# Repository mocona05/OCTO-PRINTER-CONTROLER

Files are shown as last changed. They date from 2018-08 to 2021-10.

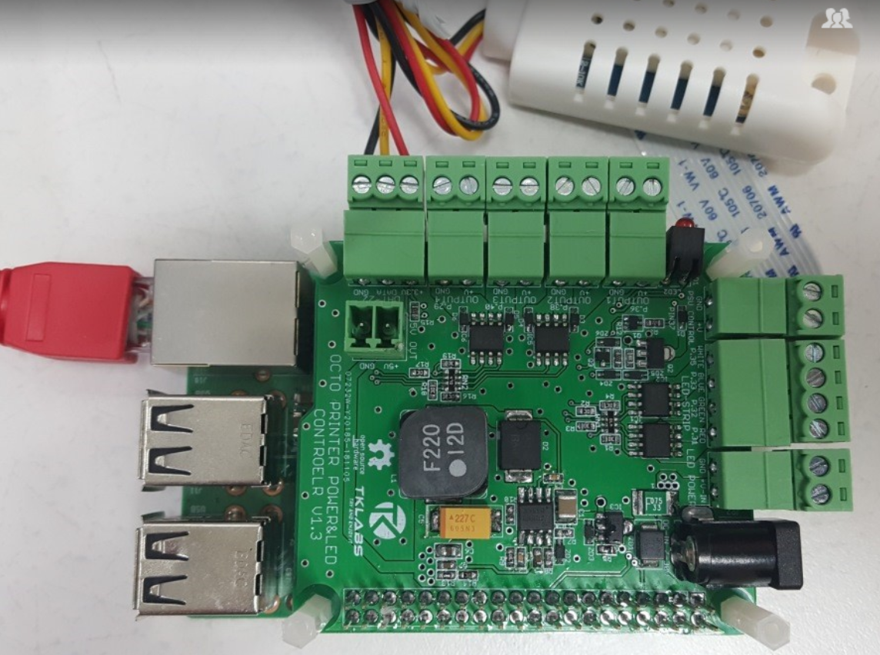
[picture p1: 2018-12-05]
image/octo printer.png

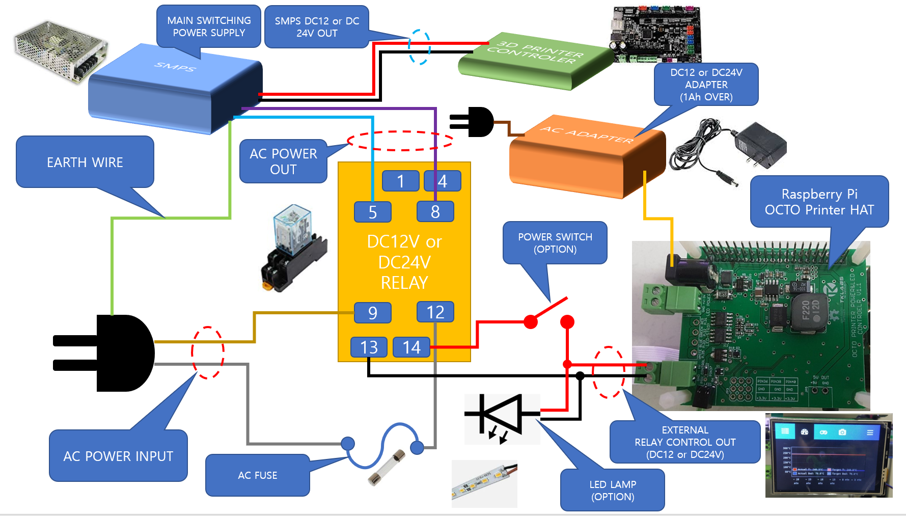
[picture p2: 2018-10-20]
image/WIRING.png

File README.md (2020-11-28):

# OCTO-PRINTER TFT-LCD HAT MOUDLE (3D PRINTER)

**1. DC 7~30V INPUT(DC12V or DC24V, 5V 4A OUT)**

**2. POWER SUPPLY UNIT CONTROL( EXTERNAL RELAY CONTROL 12V or 24V Relay)**

**3. RGBW LED STRIP CONTROL(RED, BLUE, GREEN, WHITE LED FET SWITCHING CONTROL)**

https://ko.aliexpress.com/item/33022691125.html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,searchweb201602_,searchweb201603_

**4. Raspberry SPI INTERFACE TFT-LCD & TOUCH SUPPORT**

https://ko.aliexpress.com/item/32233522592.html?spm=a2g0s.9042311.0.0.5f7c4c4dNYOjiv

**5. ENCLOSURE-CONTROL SUPPORT (HUMIDITY, TEMPERATURE MONITORING, OUTPUT RELAY 4CHANNEL CONTROL SUPPORT)**

**6. Raspberry Pi AP Cooling FAN(5V, PWM Speed Control)**

**7. Klipper ADXL345 Sensor Connector Bulit in(ADXL345 resonance sensor cannot be used simultaneously with SPI-LCD.)**

https://www.klipper3d.org/Measuring_Resonances.html

For more information, see WIKI.<br>
https://github.com/mocona05/OCTO-PRINTER-CONTROLER/wiki

Application of Octo Printer Shiled<br>
https://www.thingiverse.com/make:639404

OCTO Controler v1 4_PCB
OCTO Controler v1 4

octo printer
octo printer2
octo printer3

v1 2_sch
pcb_v1 2
wiring

v1 1_01
LCD module Pi TFT 3.5 inch (320*480) Touchscreen Display Module
v1 1_03
v1 1_02
v1 1_06
v1 1_v04
v1 1_v05
v1 1_v07
v1 1_v10

**TOUCH GHI SETTING**

OCTO PRINTER IMAGE DOWN LOAD
https://octoprint.org/download/

OCTO PRINTER IMAGE to SD MEMORY WRITE

https://www.raspberrypi.org/forums/viewtopic.php?t=131489
https://www.raspberrypi.org/forums/viewtopic.php?p=890408#p890408

**RASPBERRY PI FIRMWARE UPDATE**

`sudo rpi-update`

**RASPBERRY PI UPDATE**

`sudo apt-get update`<br>
`sudo apt-get upgrade`<br>

**RASPBERRY PI XWINDOWS INSTALL**

`sudo apt-get install --no-install-recommends xserver-xorg`<br>
`sudo apt-get install --no-install-recommends xinit`<br>
`sudo apt-get install raspberrypi-ui-mods`<br>

**xwindos auto login & Pi camera setting**

`sudo raspi-config`<br>
3.Boot-option -> B1 Desktop /CLI -> B4 Desktop Autologin

rpi-set01

Pi CAMERA SETUP (Raspberry pi camera used)
5. Interfacing Optin -> Pi Camera -> Yes
rpi-set02

7.Advanced Options -> A1 Expand Filesystem
rpi-set03

**TFT DRIVER INSTALL**

https://www.waveshare.com/wiki/3.5inch_RPi_LCD_(A)#Method_1._Driver_installation

`wget https://www.waveshare.com/w/upload/1/1e/LCD-show-180817.tar.gz`<br>

consol1

**DRIVER extractor**

`tar xvf LCD-show-180817.tar.gz`<br>
`cd LCD-show/`<br>
`chmod 777 LCD35-show`<br>
`./LCD35-show`<br>

**HDMI & TOUCH DRIVER INSTALL**

https://www.raspberrypi.org/forums/viewtopic.php?t=175616

`sudo apt-get install xinput-calibrator`<br>

**CHROMIUM INSTALL**

`sudo apt-get install unclutter`<br>
`sudo apt-get install xdotool`<br>

https://raspberrypi.stackexchange.com/questions/374/how-do-i-install-google-chrome

`sudo apt-get install chromium-browser`<br>

**CHROMIUM AUTO START SETTING**

https://www.raspberrypi.org/forums/viewtopic.php?t=163316

`sudo nano ~/.config/lxsession/LXDE-pi/autostart`<br>
`sudo -u pi chromium-browser --kiosk --incognito http://127.0.0.1 &`<br>

consol2

`sudo reboot`

connect at http://<your Raspberry pi's IP>

**PSU Control Plug In Setup**

gui01

**LED Strip Control Plug in Setup**

gui02

**TouchUI Plug in Setup**

gui03

**USB CAM Install(Option)**

https://github.com/jacksonliam/mjpg-streamer/

`sudo apt-get install subversion libjpeg8-dev libav-tools libv4l-dev cmake`<br>
`git clone https://github.com/jacksonliam/mjpg-streamer.git`<br>
`cd mjpg-streamer/mjpg-streamer-experimental`<br>
`export LD_LIBRARY_PATH=.`<br>
`sudo make`<br>

Connecting camera repeat command.

`ls /dev/video*`<br> 
(If you see the / dev / video0, then everything should be fine, go ahead)

ttps://github.com/foosel/OctoPrint/wiki/MJPG-Streamer-configuration

`sudo ./mjpg_streamer –i "./input_uvc.so –f 2 -y" -o "./output_http.so"`

check at http://<your Raspberry pi's IP>:8080/?action=stream

cam1

`sudo usermod -a -G video pi`<br>
(to allow user access to a device video, it is necessary to add it to the appropriate group)

`sudo make install`<br>
`cd ~`<br>
`sudo nano webcam-streamer`<br>

`#!/bin/bash`<br>
`Daemon=mjpg_streamer`<br>
`DaemonBase=/usr/local`<br>
`DaemonArgs="-i \"input_uvc.so –f 2 -y\" -o \"output_http.so\""`<br>
`case "" in`<br>
`start)`<br>
`eval LD_LIBRARY_PATH=${DaemonBase}/lib ${DaemonBase}/bin/${Daemon} ${DaemonArgs} >/dev/null 2>&1 &`<br>
`echo ": started"`<br>
`;;`<br>
`stop)`<br>
`pkill -x ${Daemon}`<br>
`echo ": stopped"`<br>
`;;`<br>
`*)`<br>
`echo "Usage:  {start|stop}" >&2`<br>
`;;`<br>
`Esac`<br>

cam02

`sudo chmod +x webcam-streamer`<br>
`sudo mv webcam-streamer /usr/local/bin/`<br>
`sudo nano ~/.octoprint/config.yaml`<br>

`system:`<br>
  `actions:`<br>
  `- action: streamon`<br>
    `command: sudo /usr/local/bin/webcam-streamer start`<br>
    `confirm: false`<br>
    `name: Start video stream`<br>
  `- action: streamoff`<br>
    `command: sudo /usr/local/bin/webcam-streamer stop`<br>
    `confirm: false`<br>
    `name: Stop video stream`<br>

cam03

cam04

**Auto start cam**

`sudo nano /etc/rc.local`<br>

`usr/local/bin/webcam-streamer start`<br>
(Just make sure to put it above the line that reads exit 0).

cam05

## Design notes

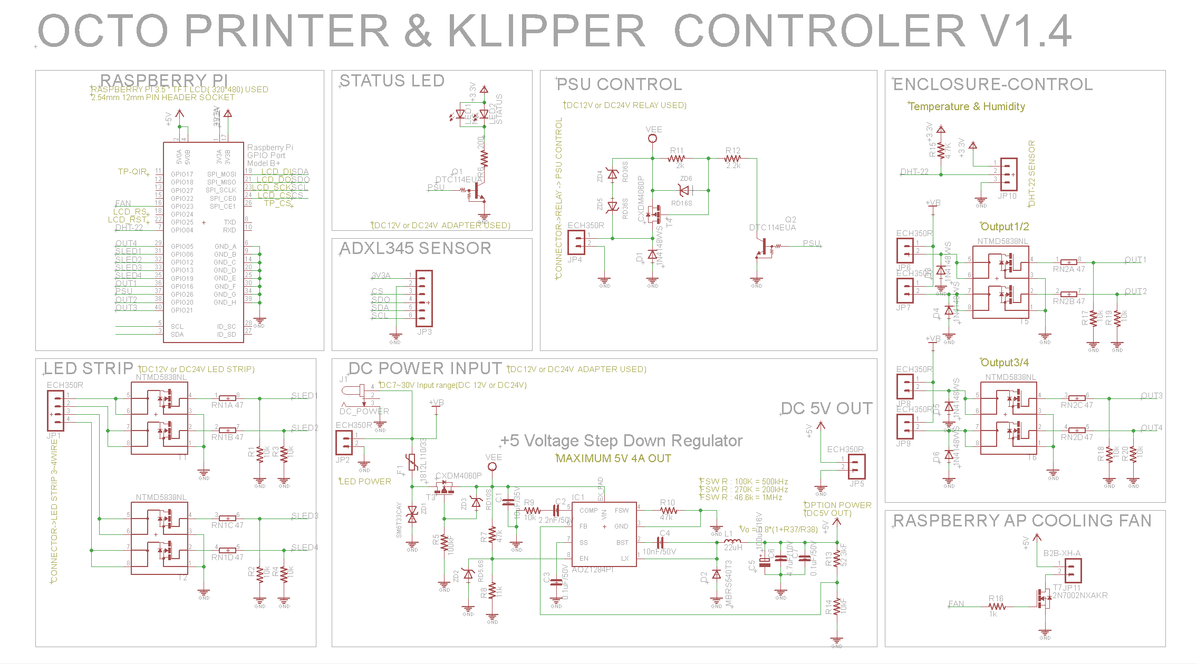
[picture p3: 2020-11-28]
image/OCTO Controler v1.4.png

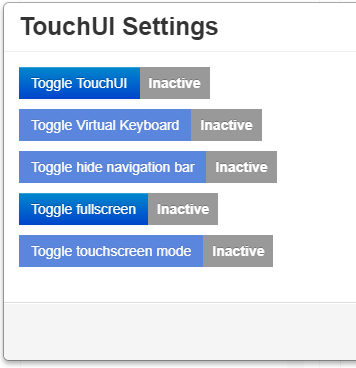
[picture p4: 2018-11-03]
image/touchUI.png

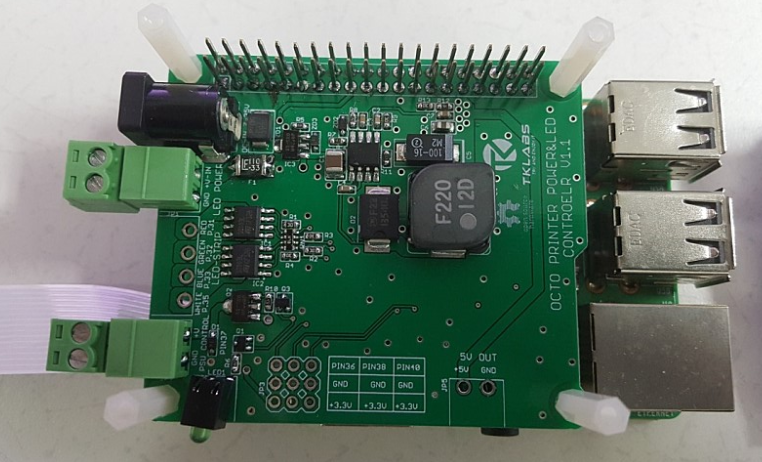
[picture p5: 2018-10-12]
image/V1.1_01.png

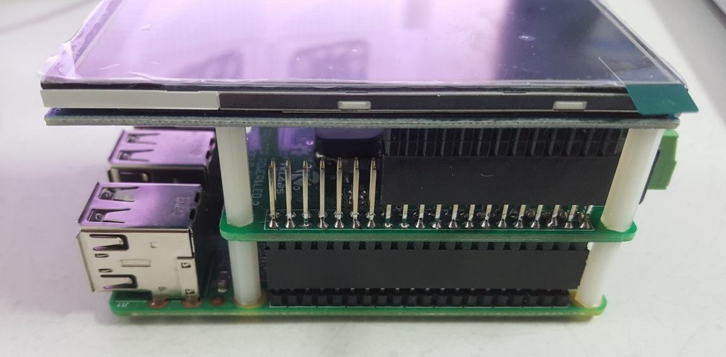
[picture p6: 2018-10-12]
image/V1.1_02.png

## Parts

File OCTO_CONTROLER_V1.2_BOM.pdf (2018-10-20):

No. | Parts | Value | Package | Device | Qty | Description
1 | R1, R2, R3, R4, R9 | 10kJ | R1608 | | 5 | SMD RESISTOR
2 | R11 | 2kJ | R1608 | | 1 | SMD RESISTOR
3 | R12 | 2.2kJ | R1608 | | 1 | SMD RESISTOR
4 | R13 | 52.3kF | R1608 | | 1 | SMD RESISTOR
5 | R5 | 100kJ | R1608 | | 1 | SMD RESISTOR
6 | R6 | 200J | R1608 | | 1 | SMD RESISTOR
7 | R7, R10 | 47kJ | R1608 | | 2 | SMD RESISTOR
8 | R8 | 11kJ | R1608 | | 1 | SMD RESISTOR
9 | R14 | 10kF | R1608 | | 1 | SMD RESISTOR
10 | RN1 | 47J | ARRAY R3216 | | 1 | ARRAY SMD RESISTOR
11 | C1 | 10uF/35V | C3225 | | 1 | CERAMIC CAP
12 | C2 | 2.2nF/50V | C1608 | | 1 | CERAMIC CAP
13 | C3 | 0.1uF/50V | C1608 | | 1 | CERAMIC CAP
14 | C4 | 10nF/50V | C1608 | | 1 | CERAMIC CAP
15 | C5 | 100uF/16V | C7343 | | 1 | TANTAL CAPACITOR
16 | C6 | 4.7uF/10V | C2012 | | 1 | CERAMIC CAP
17 | C7 | 0.1uF | C1608 | | 1 | CERAMIC CAP
18 | D1 | 1N4148WS | SOD323 | | 1 | DIODE
19 | D2 | MBRS540T3 | SMC | | 1 | SCHOTTKY DIODE
20 | ZD1 | SM6T33CAY | SMB | | 1 | TVS DIODE 33V
21 | ZD2 | RD5.6S | DSMM | | 1 | ZENER DIODE 5.6V
22 | ZD3 | RD10S | DSMM | | 1 | ZENER DIODE 47V
23 | ZD4, ZD5 | RD36S | DSMM | | 2 | ZENER DIODE 47V
24 | ZD6 | RD16S | DSMM | | 1 | ZENER DIODE 47V
25 | LED1 | NC | LED-1608 | | 1 | NOT SMD
26 | LED2 | 3FG2HD-T1 | | RED LED | 1 | BOARD MOUNT LED
27 | F1 | 1812L110/33 | 1812L | | 1 | POLY FUSE(HOLD 1.1A, MAX 33V)
28 | IC1, IC2 | NTMD5838NL | SO08 | | 2 | DUAL CHANNEL N-CH MOS FET
29 | IC3, Q2 | CXDM4060P | SOT89 | | 2 | P-CH MOS FET
30 | IC4 | AOZ1284PI | S08-EP1 | | 1 | SWITCHING REGULATOR
31 | L1 | 22uH | SHP1260P-F | | 1 | POWER INDUCTOR
32 | Q1, Q3 | DTC114EUA | SC59-BEC | | 2 | NPN Bias Resistor Transistor
33 | X1 | | 2.54mm DUAL *40PIN, 12mm | | 1 | 2.54mm DUAL PIN HEADER SOCKET 12mm
34 | J1 | | DC-005 | | 1 | DC JACK φ5.5mm
35 | JP2, JP4, JP5 | ECH350R-02 | 3.5mm PITCH 2PIN | | 3 | DINKLE PINHEADER 2PIN
36 | JP3 | 3*3, 2.54mm | 2.54mm PIN HEADER | PIN HEADER 3*3 | 1 | 3*3, 2.54mm RIGHT ANGLE PIN HEADER
37 | JP1 | ECH350R-04 | 3.5mm PITCH 3PIN | | 1 | DINKLE PINHEADER 4PIN
38 | | EC350V-02 | | | 3 | DINKLE CONNECTOR 2PIN
39 | | EC350V-04 | | | 1 | DINKLE CONNECTOR 4PIN
40 | TFT LCD | | | | 1 | 3.5 INCHI RASPBERRY LCD(320*480)
41 | PCB SUPPORT | 15mm | | | 4 | PCB SUPPORT M2
42 | PCB SUPPORT | 18mm | | | 4 | PCB SUPPORT M2

## OCTO PRINTER SHILED V1.2 BOM

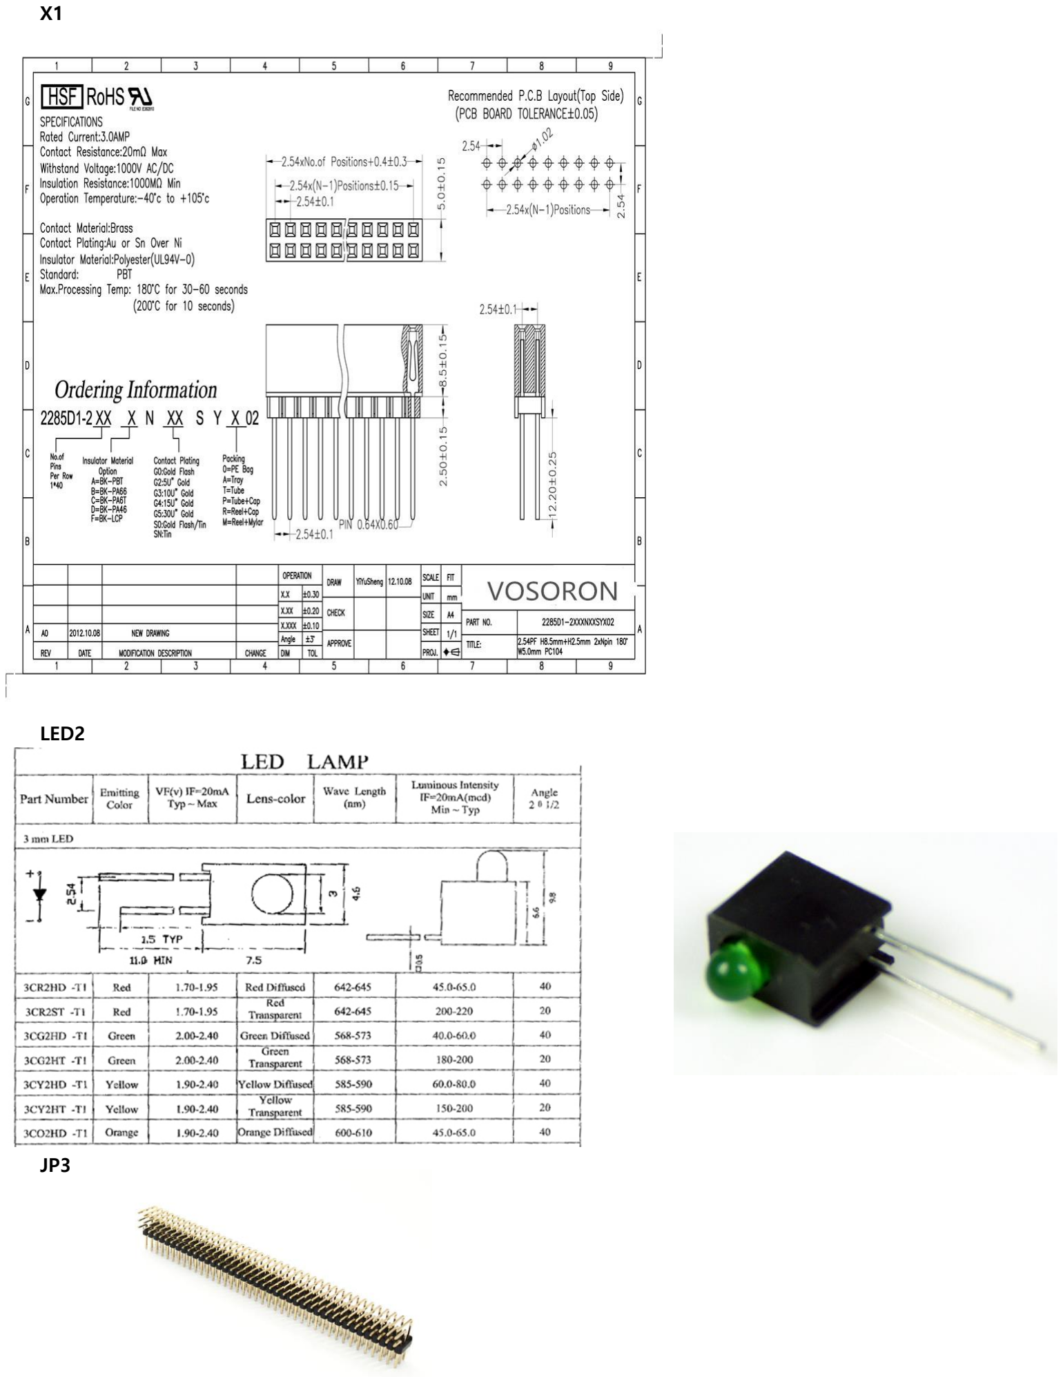
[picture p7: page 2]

X1

LED2

JP3 http://www.littelfuse.com/products/resettable-ptcs/surface-mount/1812l/1812l110_33.aspx

http://huijia-tech.com/upload/1230002737x-636397003.pdf

https://www.aliexpress.com/item/2PCS-2x40-PIN-double-Row-Straight-FEMALE-PIN-HEADER-2-54MM-PITCH-pin-long-12MM-Strip/32868136637.html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 (https://www.aliexpress.com/item/2PCS-2x40-PIN-double-Row-Straight-FEMALE-PIN-HEADER-2-54MM-PITCH-pin-long-12MM-Strip/32868136637.html)

https://www.dinkle.com/kr/terminal/ECH350R-XXPhttps://www.aliexpress.com/item/5Pcs-Gold-Plated-Pitch-2-54mm-3x40-Pin-120-Pin-Right-Angle-Male-Pin-Header-Strip/327023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 (https://www.aliexpress.com/item/5Pcs-Gold-Plated-Pitch-2-54mm-3x40-Pin-120-Pin-Right-Angle-Male-Pin-Header-Strip/32702387665.html) https://www.aliexpress.com/item/2PCS-2x40-PIN-double-Row-Straight-FEMALE-PIN-HEADER-2-54MM-PITCH-pin-long-12MMhttps://www.dinkle.com/en/terminal/EC350V-XXP

https://www.aliexpress.com/item/Free-shipping-LCD-module-Pi-TFT-3-5-inch-320-480-Touchscreen-Display-Module-TFT-for/32233522592.html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

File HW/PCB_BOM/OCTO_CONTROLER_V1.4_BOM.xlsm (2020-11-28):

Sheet: OCTO_CONTROLER_V1.2
OCTO PRINTER HAT V1.2 BOM
9f . V | Parts | Value | Package | Device | Qty | Description
1 | R1, R2, R3, R4, R9 | 10kJ | R1608 |  | 5 | SMD RESISTOR
2 | R11 | 2kJ | R1608 |  | 1 | SMD RESISTOR
3 | R12 | 2.2kJ | R1608 |  | 1 | SMD RESISTOR
4 | R13 | 52.3kF | R1608 |  | 1 | SMD RESISTOR
5 | R5 | 100kJ | R1608 |  | 1 | SMD RESISTOR
6 | R6 | 200J | R1608 |  | 1 | SMD RESISTOR
7 | R7, R10 | 47kJ | R1608 |  | 2 | SMD RESISTOR
8 | R8 | 11kJ | R1608 | sdf;m | 1 | SMD RESISTOR
9 | R14 | 10kF | R1608 |  | 1 | SMD RESISTOR
10 | RN1 | 47J | ARRAY R3216 |  | 1 | ARRAY SMD RESISTOR
11 | C1 | 10uF/35V | C3225 |  | 1 | CERAMIC CAP
12 | C2 | 2.2nF/50V | C1608 |  | 1 | CERAMIC CAP
13 | C3 | 0.1uF/50V | C1608 |  | 1 | CERAMIC CAP
14 | C4 | 10nF/50V | C1608 |  | 1 | CERAMIC CAP
15 | C5 | 100uF/16V | C7343 |  | 1 | TANTAL CAPACITOR
16 | C6 | 4.7uF/10V | C2012 |  | 1 | CERAMIC CAP
17 | C7 | 0.1uF | C1608 |  | 1 | CERAMIC CAP
18 | D1 | 1N4148WS | SOD323 |  | 1 | DIODE
19 | D2 | MBRS540T3 | SMC |  | 1 | SCHOTTKY DIODE
20 | ZD1 | SM6T33CAY | SMB |  | 1 | TVS DIODE 33V
21 | ZD2 | RD5.6S | DSMM |  | 1 | ZENER DIODE 5.6V
22 | ZD3 | RD10S | DSMM |  | 1 | ZENER DIODE 47V
23 | ZD4, ZD5 | RD36S | DSMM |  | 2 | ZENER DIODE 47V
24 | ZD6 | RD16S | DSMM |  | 1 | ZENER DIODE 47V
~~25~~ | ~~LED1~~ | ~~NC~~ | ~~LED-1608~~ |  | ~~1~~ | ~~NOT SMD~~
26 | LED2 | 3FG2HD-T1 |  | RED LED | 1 | BOARD MOUNT LED
27 | F1 | 1812L110/33 | 1812L |  | 1 | POLY FUSE(HOLD 1.1A, MAX 33V) | http://www.littelfuse.com/products/resettable-ptcs/surface-mount/1812l/1812l110_33.aspx
28 | IC1, IC2 | NTMD5838NL | SO08 |  | 2 | DUAL CHANNEL N-CH MOS FET
29 | IC3, Q2 | CXDM4060P | SOT89 |  | 2 | P-CH MOS FET
30 | IC4 | AOZ1284PI | S08-EP1 |  | 1 | SWITCHING REGULATOR
31 | L1 | 22uH | SHP1260P-F |  | 1 | POWER INDUCTOR | http://huijia-tech.com/upload/1230002737x-636397003.pdf
32 | Q1, Q3 | DTC114EUA | SC59-BEC |  | 2 | NPN Bias Resistor Transistor
33 | X1 |  | 2.54mm DUAL *40PIN, 12mm |  | 1 | 2.54mm DUAL PIN HEADER SOCKET 12mm | https://www.aliexpress.com/item/2PCS-2x40-PIN-double-Row-Straight-FEMALE-PIN-HEADER-2-54MM-PITCH-pin-long-12MM-Strip/32868136637.html
34 | J1 |  | DC-005 |  | 1 | DC JACK φ5.5mm
35 | JP2, JP4, JP5 | ECH350R-02 | 3.5mm PITCH 2PIN |  | 3 | DINKLE PINHEADER 2PIN | https://www.dinkle.com/kr/terminal/ECH350R-XXP
36 | JP3 | 3*3, 2.54mm | 2.54mm PIN HEADER | PIN HEADER 3*3 | 1 | 3*3, 2.54mm RIGHT ANGLE PIN HEADER | https://www.aliexpress.com/item/5Pcs-Gold-Plated-Pitch-2-54mm-3x40-Pin-120-Pin-Right-Angle-Male-Pin-Header-Strip/32702387665.html
37 | JP1 | ECH350R-04 | 3.5mm PITCH 3PIN |  | 1 | DINKLE PINHEADER 4PIN | https://www.aliexpress.com/item/2PCS-2x40-PIN-double-Row-Straight-FEMALE-PIN-HEADER-2-54MM-PITCH-pin-long-12MM-Strip/32868136637.html
38 |  | EC350V-02 |  |  | 3 | DINKLE CONNECTOR 2PIN | https://www.dinkle.com/en/terminal/EC350V-XXP
39 |  | EC350V-04 |  |  | 1 | DINKLE CONNECTOR 4PIN
40 | TFT LCD |  |  |  | 1 | 3.5 INCHI RASPBERRY LCD(320*480) | https://www.aliexpress.com/item/Free-shipping-LCD-module-Pi-TFT-3-5-inch-320-480-Touchscreen-Display-Module-TFT-for/32233522592.html
41 | PCB SUPPORT | 15mm |  |  | 4 | PCB SUPPORT M2
42 | PCB SUPPORT | 18mm |  |  | 4 | PCB SUPPORT M2
 | X1
 | LED2
 | JP3

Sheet: OCTO_CONTROLER_V1.3
OCTO PRINTER HAT V1.4 BOM
No. | Parts | Value | Package | Device | Qty | Description
1 | R1, R2, R3, R4, R9, R17, R18, R19, R20 | 10kJ | R1608 |  | 9 | SMD RESISTOR
2 | R11 | 2kJ | R1608 |  | 1 | SMD RESISTOR
3 | R12 | 2.2kJ | R1608 |  | 1 | SMD RESISTOR
4 | R13 | 52.3kF | R1608 |  | 1 | SMD RESISTOR
5 | R5 | 100kJ | R1608 |  | 1 | SMD RESISTOR
6 | R6 | 200J | R1608 |  | 1 | SMD RESISTOR
7 | R7, R10 | 47kJ | R1608 |  | 2 | SMD RESISTOR
8 | R8 | 11kJ | R1608 | sdf;m | 1 | SMD RESISTOR
9 | R14 | 10kF | R1608 |  | 1 | SMD RESISTOR
10 | R15 | 4.7k | R1608 |  | 1 | SMD RESISTOR
11 | R16 | 1k | R1608 |  | 1 | SMD RESISTOR
12 | RN1, RN2 | 47J | ARRAY R3216 |  | 2 | ARRAY SMD RESISTOR
13 | C1 | 10uF/35V | C3225 |  | 1 | CERAMIC CAP
14 | C2 | 2.2nF/50V | C1608 |  | 1 | CERAMIC CAP
15 | C3, C7 | 0.1uF/50V | C1608 |  | 2 | CERAMIC CAP
16 | C4 | 10nF/50V | C1608 |  | 1 | CERAMIC CAP
17 | C5 | 100uF/16V | C7343 |  | 1 | TANTAL CAPACITOR
18 | C6 | 4.7uF/10V | C2012 |  | 1 | CERAMIC CAP
19 | D1 | 1N4148WS | SOD323 |  | 1 | DIODE
20 | D2 | MBRS540T3 | SMC |  | 1 | SCHOTTKY DIODE
21 | ZD1 | SM6T33CAY | SMB |  | 1 | TVS DIODE 33V
22 | ZD2 | RD5.6S | DSMM |  | 1 | ZENER DIODE 5.6V
23 | ZD3 | RD10S | DSMM |  | 1 | ZENER DIODE 47V
24 | ZD4, ZD5 | RD36S | DSMM |  | 2 | ZENER DIODE 47V
25 | ZD6 | RD16S | DSMM |  | 1 | ZENER DIODE 47V
26 | ~~LED1~~ | ~~NC~~ | ~~LED-1608~~ |  | ~~1~~ | ~~NOT SMD~~
27 | LED2 | 3FG2HD-T1 |  | RED LED | 1 | BOARD MOUNT LED
28 | F1 | 1812L110/33 | 1812L |  | 1 | POLY FUSE(HOLD 1.1A, MAX 33V) | http://www.littelfuse.com/products/resettable-ptcs/surface-mount/1812l/1812l110_33.aspx
29 | T1, T2, T5, T6 | NTMD5838NL | SO08 |  | 4 | DUAL CHANNEL N-CH MOS FET
30 | T3, T4 | CXDM4060P | SOT89 |  | 2 | P-CH MOS FET
31 | T7 | 2N7002NXAKR | SOT23 |  | 2 | N-CH MOS FET
32 | IC1 | AOZ1284PI | S08-EP1 |  | 1 | SWITCHING REGULATOR
33 | L1 | 22uH | SHP1260P-F |  | 1 | POWER INDUCTOR | http://huijia-tech.com/upload/1230002737x-636397003.pdf
34 | Q1, Q2 | DTC114EUA | SC59-BEC |  | 2 | NPN Bias Resistor Transistor
35 | X1 |  | 2.54mm DUAL *40PIN, 12mm |  | 1 | 2.54mm DUAL PIN HEADER SOCKET 12mm | https://www.aliexpress.com/item/2PCS-2x40-PIN-double-Row-Straight-FEMALE-PIN-HEADER-2-54MM-PITCH-pin-long-12MM-Strip/32868136637.html
36 | J1 |  | DC-005 |  | 1 | DC JACK φ5.5mm
37 | JP2, JP4, JP5, JP6, JP7, JP8, JP9 | ECH350R-02 | 3.5mm PITCH 2PIN |  | 5 | DINKLE PINHEADER 2PIN | https://www.dinkle.com/kr/terminal/ECH350R-XXP
38 | JP3 | 3*3, 2.54mm | 2.54mm PIN HEADER | PIN HEADER 3*3 | 1 | 3*3, 2.54mm RIGHT ANGLE PIN HEADER | https://www.aliexpress.com/item/5Pcs-Gold-Plated-Pitch-2-54mm-3x40-Pin-120-Pin-Right-Angle-Male-Pin-Header-Strip/32702387665.html
39 | JP1 | ECH350R-04 | 3.5mm PITCH 3PIN |  | 1 | DINKLE PINHEADER 4PIN | https://www.aliexpress.com/item/2PCS-2x40-PIN-double-Row-Straight-FEMALE-PIN-HEADER-2-54MM-PITCH-pin-long-12MM-Strip/32868136637.html
40 | JP11 | B2B-XH-A | 2.54mm JST XH |  | 1 | JST 2.52mm 2PIN
41 |  | EC350V-02 |  |  | 6 |  | https://www.dinkle.com/en/terminal/EC350V-XXP
42 |  | EC350V-03 |  |  | 1 | DINKLE CONNECTOR 4PIN
43 |  | EC350V-04 |  |  | 1 | DINKLE CONNECTOR 4PIN
44 | TFT LCD |  |  |  | 1 | 3.5 INCHI RASPBERRY LCD(320*480) | https://www.aliexpress.com/item/Free-shipping-LCD-module-Pi-TFT-3-5-inch-320-480-Touchscreen-Display-Module-TFT-for/32233522592.html
45 | PCB SUPPORT | 15mm |  |  | 4 | PCB SUPPORT M2
46 | PCB SUPPORT | 18mm |  |  | 4 | PCB SUPPORT M2
 | X1
 | LED2
 | JP3
 | B2B-XH-A
 | ADXL345 SENSOR
 | https://ko.aliexpress.com/item/4000196862769.html

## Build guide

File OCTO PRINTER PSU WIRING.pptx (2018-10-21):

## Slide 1

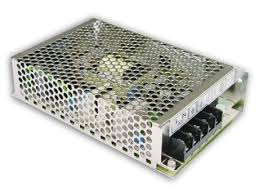
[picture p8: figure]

MAIN SWITCHING POWER SUPPLY

SMPS

SMPS DC12 or DC 24V OUT

3D PRINTER CONTROLER

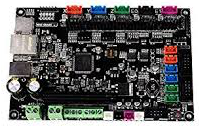
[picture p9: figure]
MKS 1.3ì ë í ì ´ë¯¸ì§ ê² ì ê²°ê³¼

DC12 or DC24V
ADAPTER
(1Ah OVER)

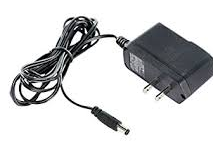
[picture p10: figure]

AC POWER OUT

AC ADAPTER

POWER SWITCH
(OPTION)

EARTH WIRE

DC12V or DC24V
RELAY

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
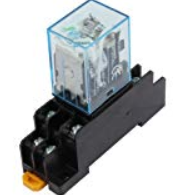
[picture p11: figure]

Raspberry Pi
OCTO Printer HAT

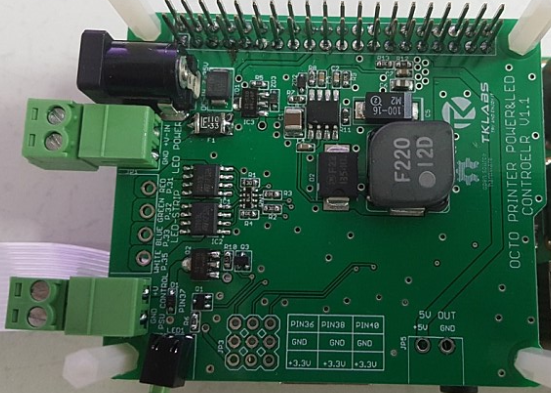
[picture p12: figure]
v1 1_01

EXTERNAL
RELAY CONTROL OUT
(DC12 or DC24V)

AC POWER INPUT

AC FUSE

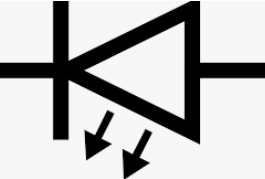
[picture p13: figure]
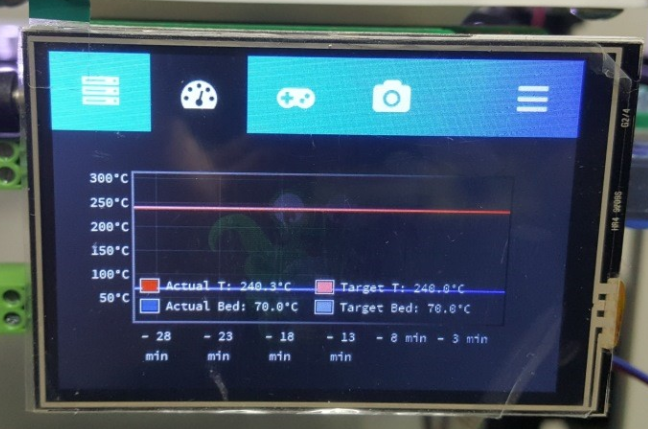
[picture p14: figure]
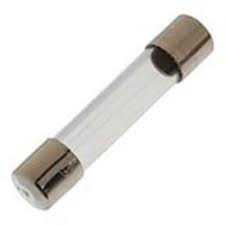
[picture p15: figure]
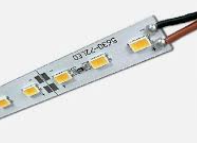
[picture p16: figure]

LED LAMP
(OPTION)

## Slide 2

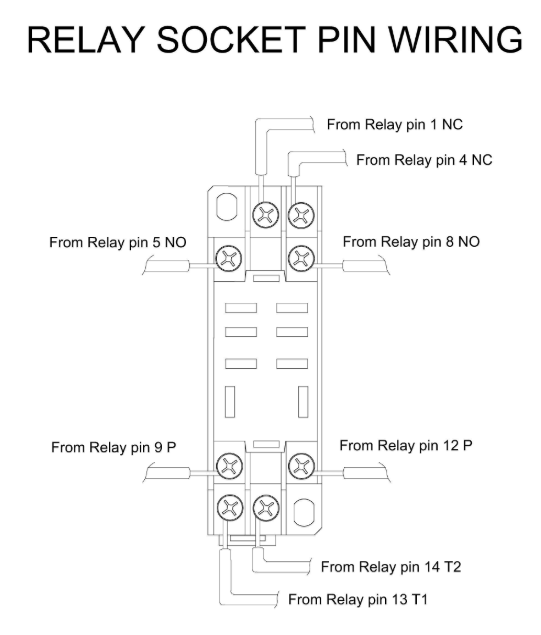
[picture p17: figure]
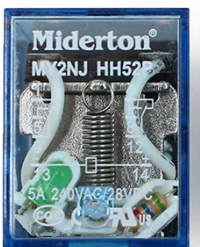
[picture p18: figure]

AC POWER OUT
(PSU UNIT)

AC POWER OUT
(PUS UNIT)

AC POWER IN
NETURAL

AC POWER IN
LIVE

+12 or 24V
(OCTO-PSU +OUT)

+12 or 24V

GND
(OCTO PI-PSU GND)

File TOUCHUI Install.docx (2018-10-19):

OCTO PRINTER IMAGE DOWN LOAD

https://octoprint.org/download/

OCTO PRINTER IMAGE to SD MEMORY WRITE

https://www.raspberrypi.org/forums/viewtopic.php?t=131489

https://www.raspberrypi.org/forums/viewtopic.php?p=890408#p890408

RASPBERRY PI FIRMWARE UPDATE

sudo rpi-update

RASPBERRY PI UPDATE

sudo apt-get update

sudo apt-get upgrade

RASPBERRY PI XWINDOWS INSTALL

sudo apt-get install --no-install-recommends xserver-xorg

sudo apt-get install --no-install-recommends xinit

sudo apt-get install raspberrypi-ui-mods

xwindos auto login & Pi camera setting

sudo raspi-config

3.Boot-option -> B1 Desktop /CLI -> B4 Desktop Autologin

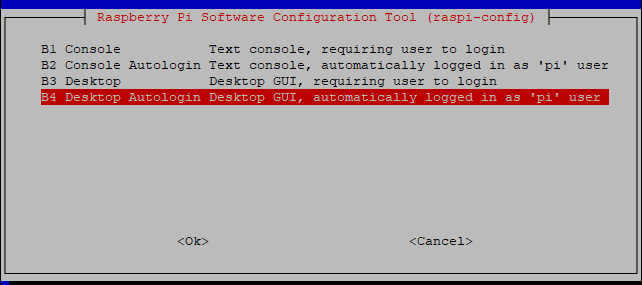
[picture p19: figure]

Pi CAMERA SETUP (Raspberry pi camera 사용시)

5. Interfacing Optin -> Pi Camera -> Yes

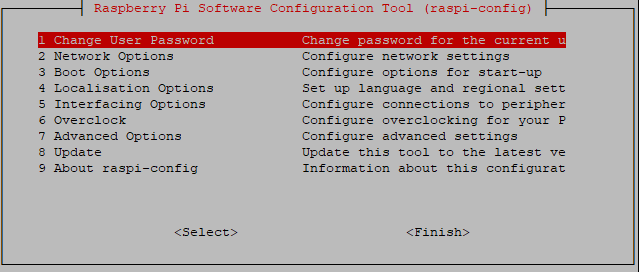
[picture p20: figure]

7.Advanced Options -> A1 Expand Filesystem

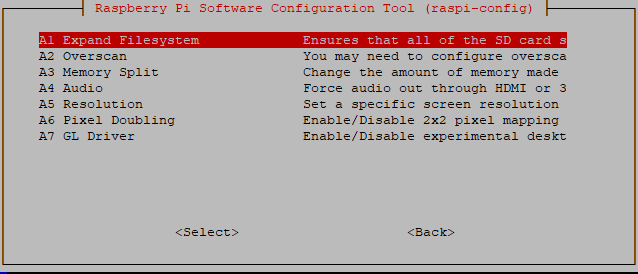
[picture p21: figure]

TFT DRIVER INSTALL

https://www.waveshare.com/wiki/3.5inch_RPi_LCD_(A)#Method_1._Driver_installation

wget https://www.waveshare.com/w/upload/1/1e/LCD-show-180817.tar.gz

DRIVER extractor

tar xvf LCD-show-180817.tar.gz

cd LCD-show/

chmod 777 LCD35-show

./LCD35-show

SPI-LCD & TOUCH DRIVER INSTALL

https://www.raspberrypi.org/forums/viewtopic.php?t=175616

sudo apt-get install xinput-calibrator

CHROMIUM INSTALL

sudo apt-get install unclutter
sudo apt-get install xdotool

https://raspberrypi.stackexchange.com/questions/374/how-do-i-install-google-chrome

sudo apt-get install chromium-browser

CHROMIUM AUTO START SETTING

https://www.raspberrypi.org/forums/viewtopic.php?t=163316

sudo nano ~/.config/lxsession/LXDE-pi/autostart

sudo -u pi chromium-browser --kiosk --incognito http://127.0.0.1 &

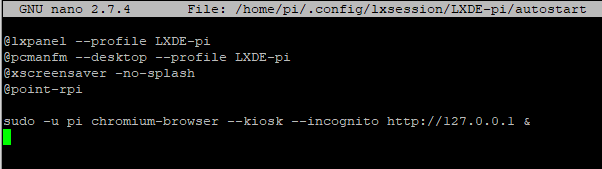
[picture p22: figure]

sudo reboot

PSU Control Plug In Setup

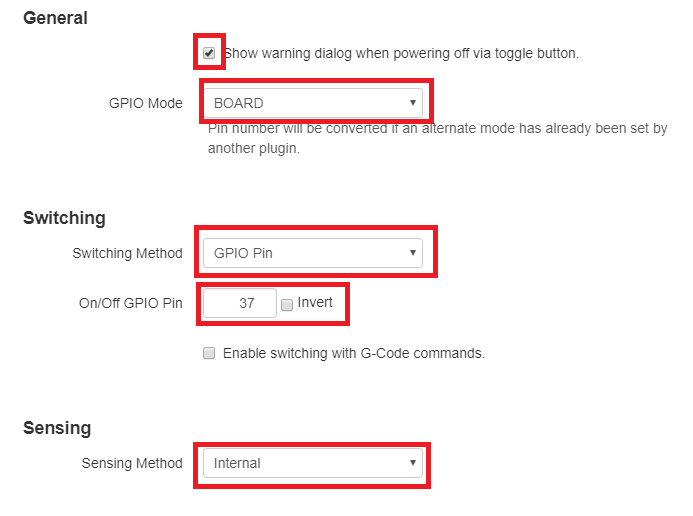
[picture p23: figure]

LED Strip Control Plug in Setup

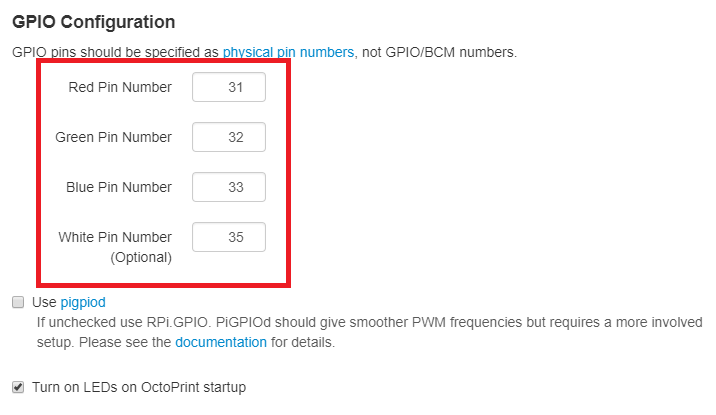
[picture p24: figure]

TouchUI Plug in Setup

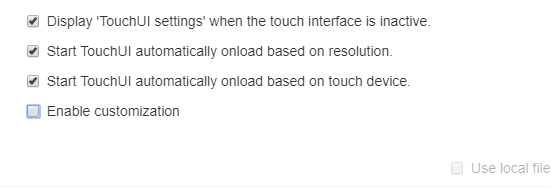
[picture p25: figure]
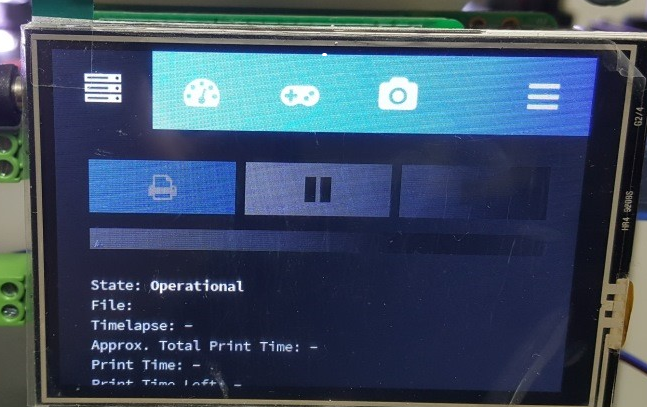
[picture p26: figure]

USB CAM Install(Option)

https://github.com/jacksonliam/mjpg-streamer/

sudo apt-get install subversion libjpeg8-dev libav-tools libv4l-dev cmake

git clone https://github.com/jacksonliam/mjpg-streamer.git

cd mjpg-streamer/mjpg-streamer-experimental

export LD_LIBRARY_PATH=.

sudo make

Connecting camera repeat command.

ls /dev/video* (If you see the / dev / video0, then everything should be fine, go ahead)

ttps://github.com/foosel/OctoPrint/wiki/MJPG-Streamer-configuration

sudo ./mjpg_streamer –i "./input_uvc.so –f 2 -y" -o "./output_http.so"

check at http://<your Raspberry pi's IP>:8080/?action=stream

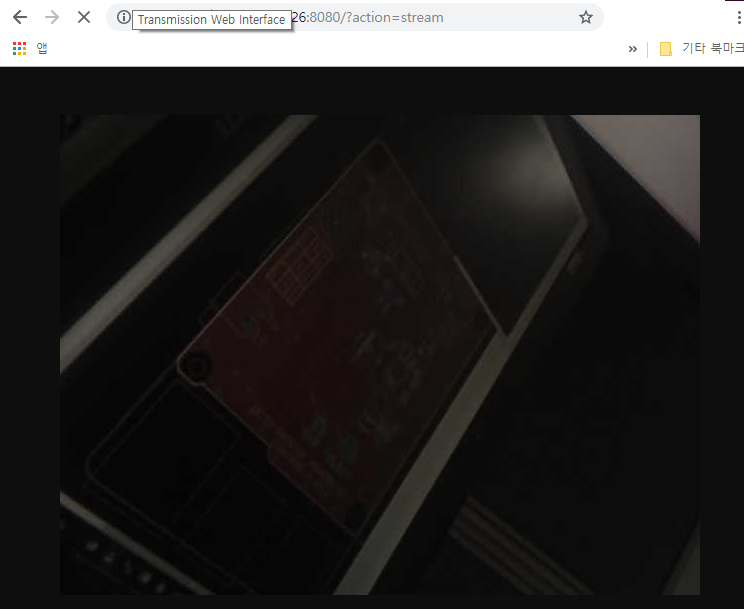
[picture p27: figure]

sudo usermod -a -G video pi

(to allow user access to a device video, it is necessary to add it to the appropriate group)

sudo make install

cd ~

sudo nano webcam-streamer

#!/bin/bash

Daemon=mjpg_streamer

DaemonBase=/usr/local

DaemonArgs="-i \"input_uvc.so –f 2 -y\" -o \"output_http.so\""

case "$1" in

start)

eval LD_LIBRARY_PATH=${DaemonBase}/lib ${DaemonBase}/bin/${Daemon} ${DaemonArgs} >/dev/null 2>&1 &

echo "$0: started"

;;

stop)

pkill -x ${Daemon}

echo "$0: stopped"

;;

*)

echo "Usage: $0 {start|stop}" >&2

;;

Esac

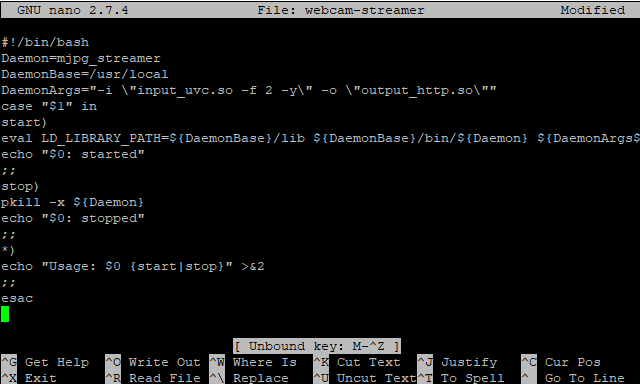
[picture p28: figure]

sudo chmod +x webcam-streamer

sudo mv webcam-streamer /usr/local/bin/

sudo nano ~/.octoprint/config.yaml

system:

actions:

- action: streamon

command: sudo /usr/local/bin/webcam-streamer start

confirm: false

name: Start video stream

- action: streamoff

command: sudo /usr/local/bin/webcam-streamer stop

confirm: false

name: Stop video stream

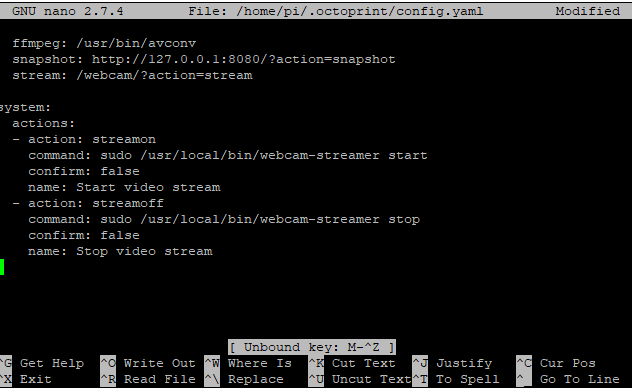
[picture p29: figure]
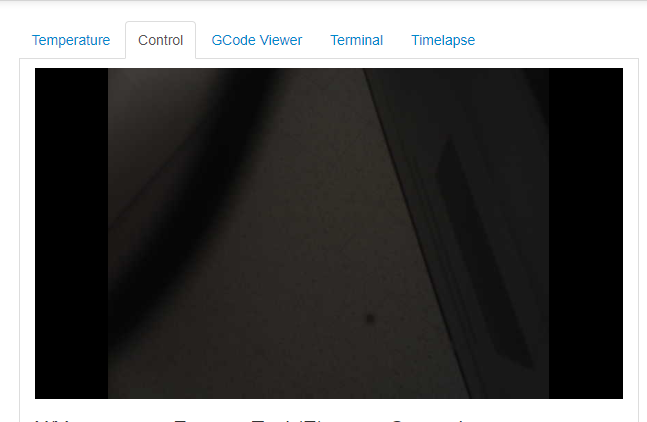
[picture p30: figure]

Auto start cam

sudo nano /etc/rc.local

usr/local/bin/webcam-streamer start

(Just make sure to put it above the line that reads exit 0).

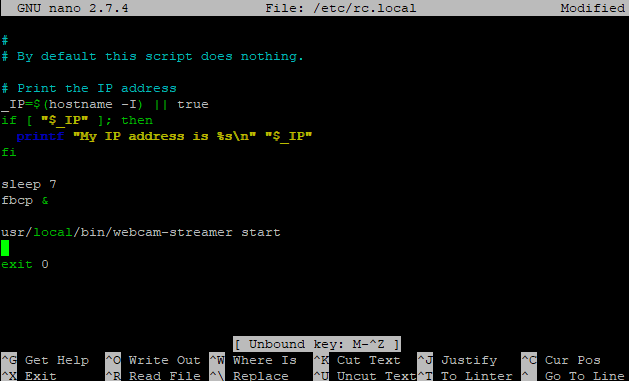
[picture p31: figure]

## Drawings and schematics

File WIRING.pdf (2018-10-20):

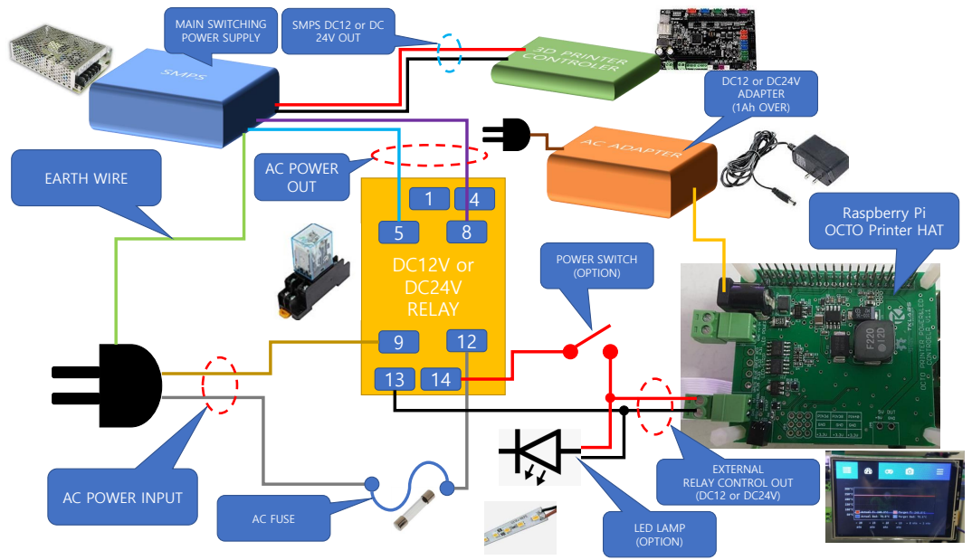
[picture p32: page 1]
DC12V or DC24V RELAY; DC12 or DC24V ADAPTER (1Ah OVER); MAIN SWITCHING POWER SUPPLY; POWER SWITCH (OPTION); AC FUSE; EARTH WIRE; AC POWER OUT; LED LAMP (OPTION)

SMPS DC12 or DC
24V OUT

Raspberry Pi
OCTO Printer HAT

EXTERNAL
RELAY CONTROL OUT

AC POWER INPUT

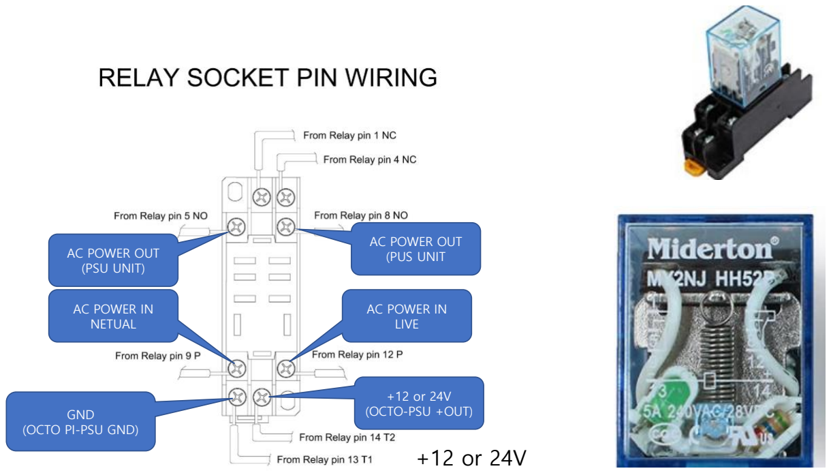
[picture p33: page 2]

# +12 or 24V

+12 or 24V
GND | (OCTO-PSU +OUT)
(OCTO PI-PSU GND)

AC POWER IN
NETUAL

AC POWER IN
LIVE

AC POWER OUT
AC POWER OUT | (PUS UNIT
(PSU UNIT)

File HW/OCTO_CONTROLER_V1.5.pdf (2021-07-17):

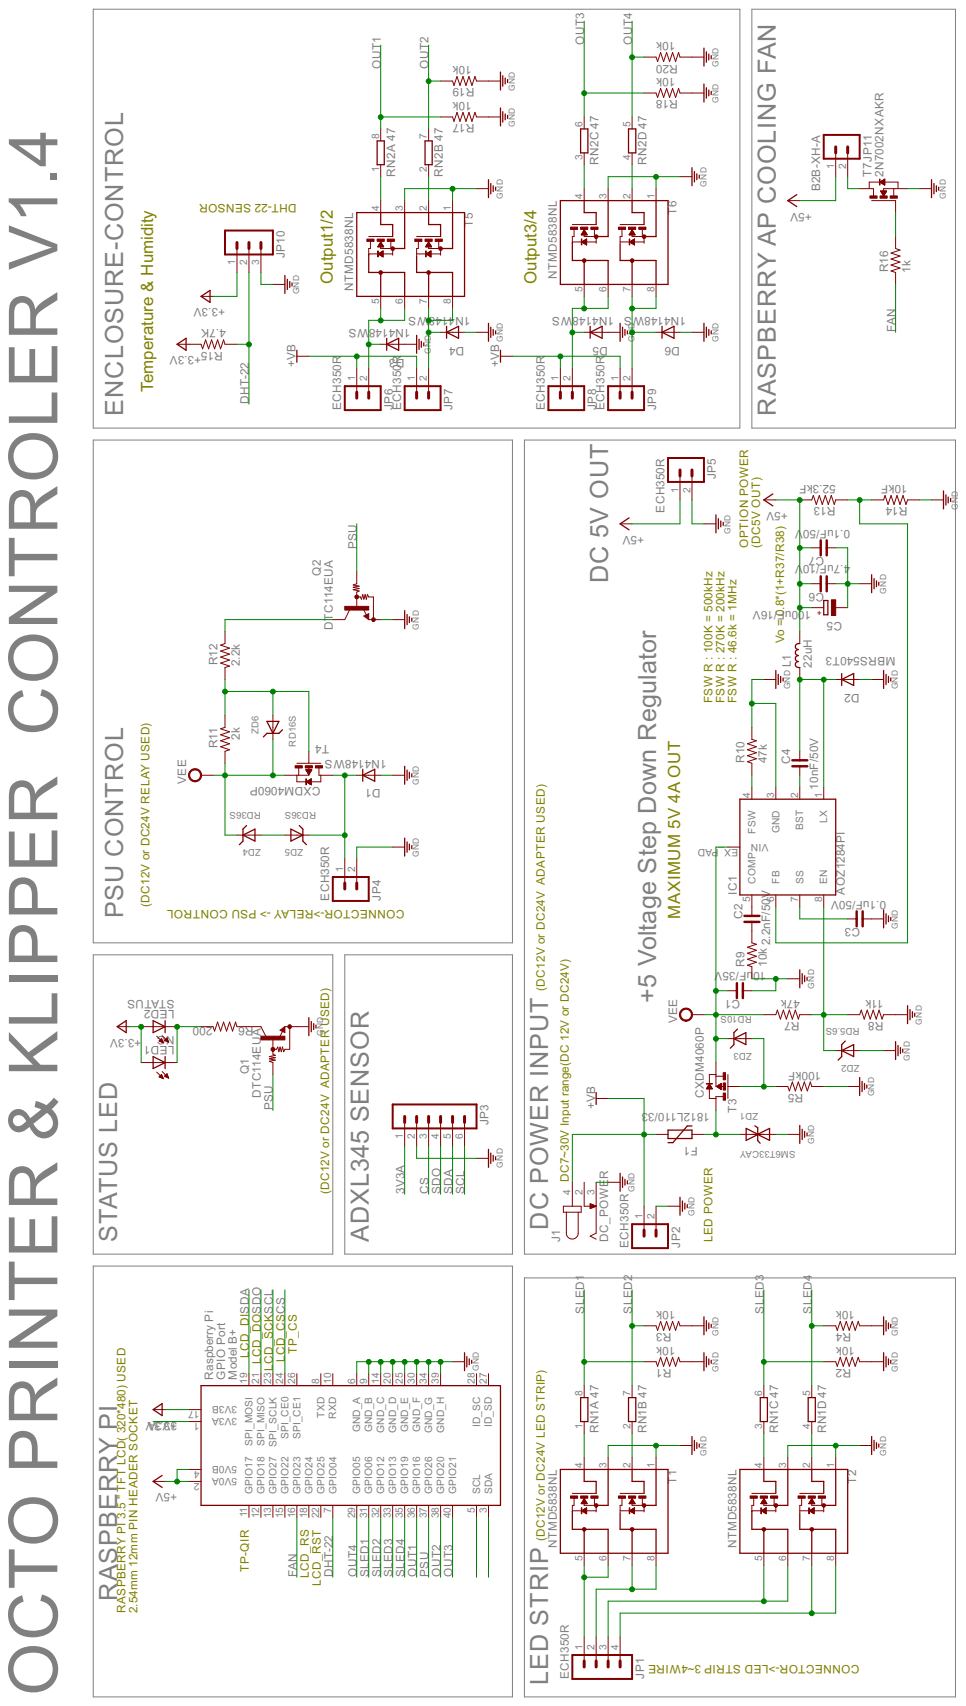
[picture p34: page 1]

2.54mm 12mm PIN HEADER SOCKET ROSNES 22- THD

GND GND

Raspberry Pi GPIO Port Model B+ 2k DTC114EUA

(DC12V or DC24V LED STRIP) (DC12V or DC24V ADAPTER USED)

DC7~30V Input range(DC 12V or DC24V)

RASPBERRY PI 3.5 " TFT LCD( 320*480) USED

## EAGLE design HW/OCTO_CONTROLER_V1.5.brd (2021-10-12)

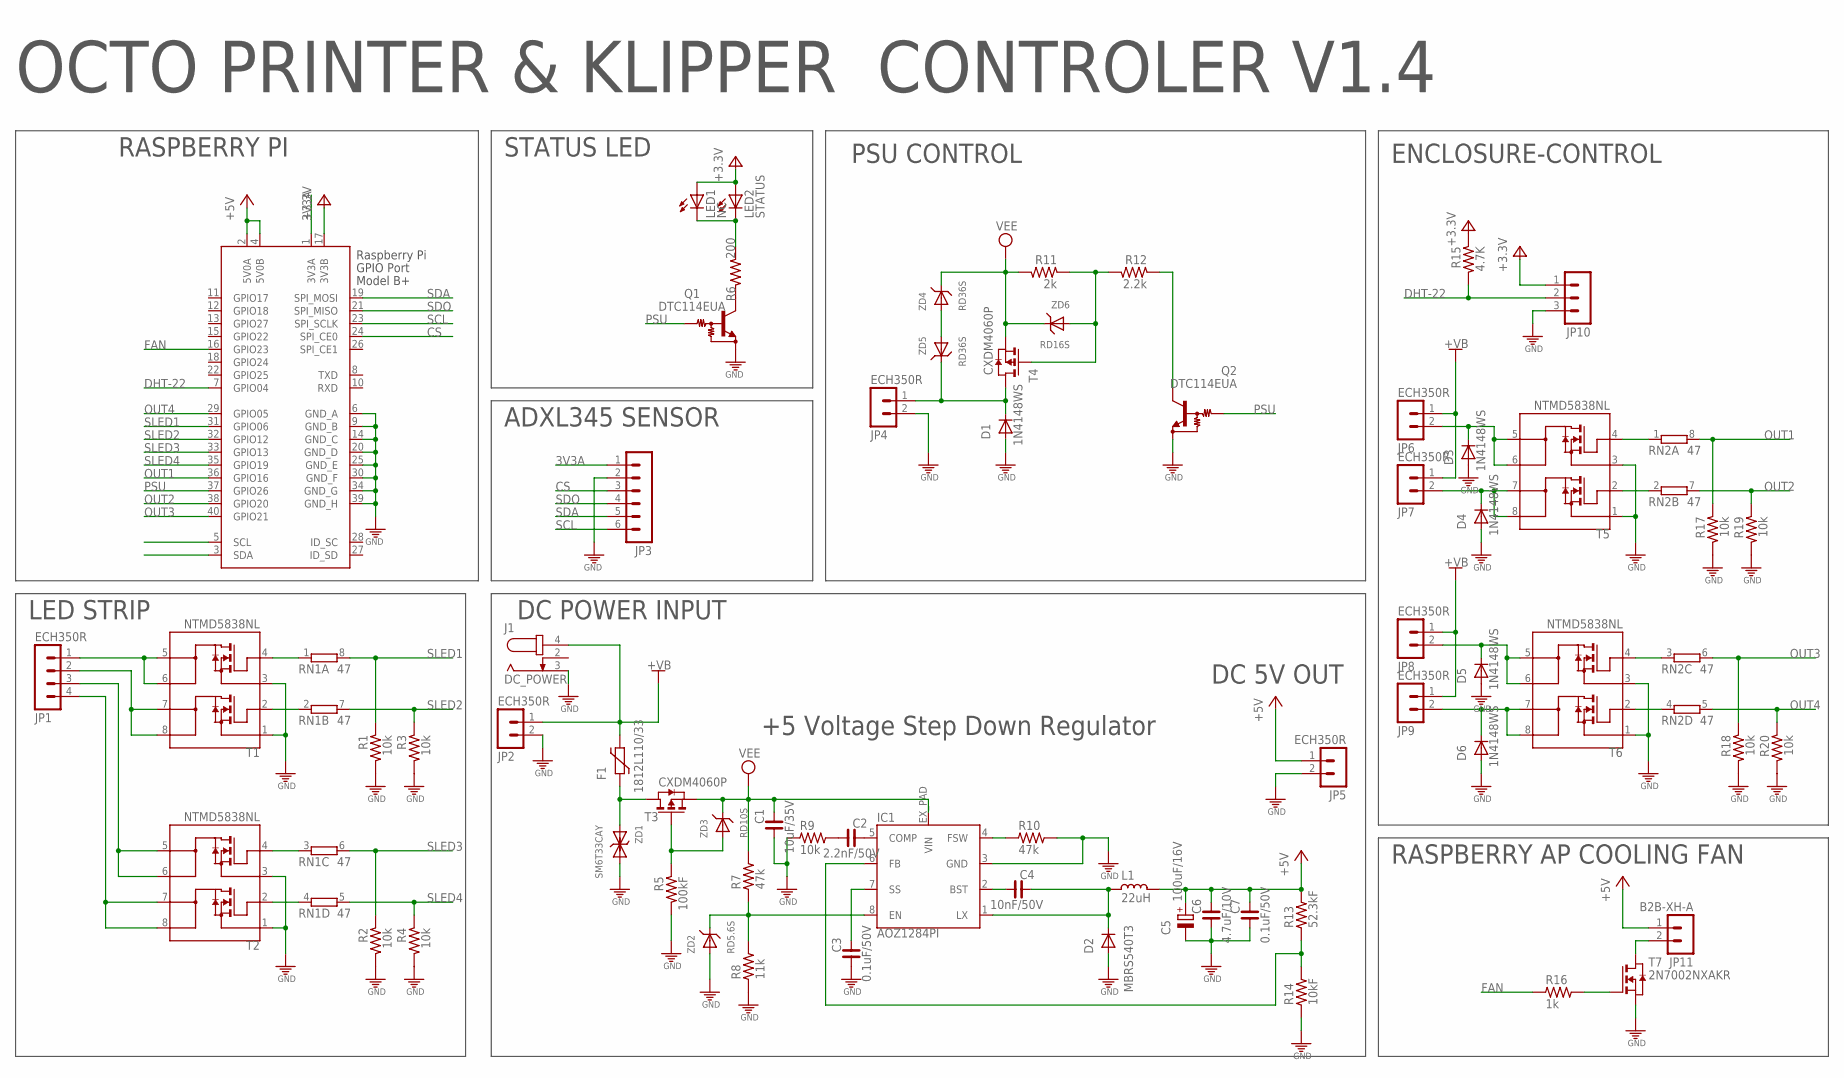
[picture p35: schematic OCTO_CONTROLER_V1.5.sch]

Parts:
C1: 10uF/35V; C3225
C2: 2.2nF/50V; C0603
C3, C7: 0.1uF/50V; C0603
C4: 10nF/50V; C0603
C5: 100uF/16V; D/7343-31W
C6: 4.7uF/10V; C2012
D1, D3, D4, D5, D6: 1N4148WS; SOD323
D2: MBRS540T3; SMC
F1: 1812L110/33; 1812L
IC1: AOZ1284PI; S08-EP1
J1: DC_POWER; DC-005
JP1: ECH350R; ECH350R-04
JP2, JP4, JP6, JP7, JP8, JP9: ECH350R; ECH350R-02
JP3: MA06-1SMALL; MA06-1-S
JP5: ECH350R; ECH350V-02
JP10: MA03-1ECH350R; ECH350R-03
JP11: B2B-XH-A; MOLEX5267-02
L1: 22uH; SHP1260P-F
LED1: NC; LED-1608
LED2: STATUS; 3FG2HD-T1
Q1, Q2: DTC114EUA; SC59-BEC
R1, R2, R3, R4, R9, R17, R18, R19, R20: 10k; R0603
R5: 100kF; R0603
R6: 200; R0603
R7, R10: 47k; R0603
R8: 11k; R0603
R11: 2k; R0603
R12: 2.2k; R0603
R13: 52.3kF; R0603
R14: 10kF; R0603
R15: 4.7K; R0603
R16: 1k; R0603
RN1, RN2: 47; ARRAY_R3216
T1, T2, T5, T6: NTMD5838NL; SO08
T3, T4: CXDM4060P; SOT89
T7: 2N7002NXAKR; SOT23
X1: RASPI_BOARD_B+#_F; RASPI_BOARD_B+_FULL
ZD1: SM6T33CAY; SMB
ZD2: RD5.6S; DSMM
ZD3: RD10S; DSMM
ZD4, ZD5: RD36S; DSMM
ZD6: RD16S; DSMM

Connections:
3V3: JP10.1, LED1.A, LED2.A, R15.1, X1.17 (3V3B)
3V3A: JP3.1, X1.1 (3V3A)
+5V: C5.+, C6.1, C7.1, JP5.1, JP11.1, L1.1, R13.2, X1.2 (5V0A), X1.4 (5V0B)
+12V: F1.P$2 (2), J1.4 (3), JP2.1, JP6.1, JP7.1, JP8.1, JP9.1
CS: JP3.3, X1.24 (SPI_CE0)
DC-IN: F1.P$1 (1), T3.2 (D), T3.2@1 (D), ZD1.A
DHT-22: JP10.2, R15.2, X1.7 (GPIO04)
FAN: R16.1, X1.16 (GPIO23)
GND: C1.2, C3.2, C5.-, C6.2, C7.2, D1.A, D2.A, D3.A, D4.A, D5.A, D6.A, IC1.3 (GND), J1.3 (1), JP2.2, JP3.2, JP4.2, JP5.2, JP10.3, Q1.1 (GND), Q2.1 (GND), R1.2, R2.2, R3.2, R4.2, R5.2, R8.1, R9.1, R10.2, R14.1, R17.2, R18.2, R19.2, R20.2, T1.1, T1.3, T2.1, T2.3, T5.1, T5.3, T6.1, T6.3, T7.S, X1.6 (GND_A), X1.9 (GND_B), X1.14 (GND_C), X1.20 (GND_D), X1.25 (GND_E), X1.30 (GND_F), X1.34 (GND_G), X1.39 (GND_H), ZD1.C (K), ZD2.A
unnamed: R11.1, R12.2, T4.3 (G), ZD6.A
unnamed: LED1.C, LED2.K (C), R6.1
unnamed: ZD4.A, ZD5.A
unnamed: RN1.2 (1), T1.2
unnamed: RN1.1, T1.4
unnamed: RN1.4 (1), T2.2
unnamed: JP11.2, T7.D
unnamed: R16.2, T7.G
unnamed: IC1.6 (FB), R13.1, R14.2
unnamed: RN1.3 (1), T2.4
unnamed: C4.2, IC1.2 (BST)
unnamed: D1.C, JP4.1, T4.2 (D), T4.2@1 (D), ZD5.C
unnamed: RN2.2 (1), T5.2
unnamed: RN2.1, T5.4
unnamed: D3.C, JP6.2, T5.5, T5.6
unnamed: D4.C, JP7.2, T5.7, T5.8
unnamed: RN2.4 (1), T6.2
unnamed: RN2.3 (1), T6.4
unnamed: C4.1, D2.C, IC1.1 (LX), L1.2
unnamed: IC1.4 (FSW), R10.1
unnamed: C3.1, IC1.7 (SS)
unnamed: IC1.8 (EN), R7.1, R8.2, ZD2.C
unnamed: C2.1, IC1.5 (COMP)
unnamed: Q2.3 (OUT), R12.1
unnamed: D5.C, JP8.2, T6.5, T6.6
unnamed: C2.2, R9.2
unnamed: D6.C, JP9.2, T6.7, T6.8
unnamed: Q1.3 (OUT), R6.2
unnamed: R5.1, T3.3 (G), ZD3.A
OUT1: R17.1, RN2.8 (2), X1.36 (GPIO16)
OUT2: R19.1, RN2.7 (2), X1.38 (GPIO20)
OUT3: R18.1, RN2.6 (2), X1.40 (GPIO21)
OUT4: R20.1, RN2.5 (2), X1.29 (GPIO05)
PSU: Q1.2 (IN), Q2.2 (IN), X1.37 (GPIO26)
S-LED1: JP1.1, T1.5, T1.6
S-LED2: JP1.2, T1.7, T1.8
S-LED3: JP1.3, T2.5, T2.6
S-LED4: JP1.4, T2.7, T2.8
SCL: JP3.6, X1.23 (SPI_SCLK)
SDA: JP3.5, X1.19 (SPI_MOSI)
SDO: JP3.4, X1.21 (SPI_MISO)
SLED1: R1.1, RN1.8 (2), X1.31 (GPIO06)
SLED2: R3.1, RN1.7 (2), X1.32 (GPIO12)
SLED3: R2.1, RN1.6 (2), X1.33 (GPIO13)
SLED4: R4.1, RN1.5 (2), X1.35 (GPIO19)
VEE: C1.1, IC1.EX_PAD (VIN), R7.2, R11.2, T3.1 (S), T4.1 (S), ZD3.C, ZD4.C, ZD6.C

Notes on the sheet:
OCTO PRINTER & KLIPPER CONTROLER V1.4
RASPBERRY PI
+5 Voltage Step Down Regulator
DC POWER INPUT
PSU CONTROL
STATUS LED
LED STRIP
DC 5V OUT
ENCLOSURE-CONTROL
ADXL345 SENSOR
RASPBERRY AP COOLING FAN

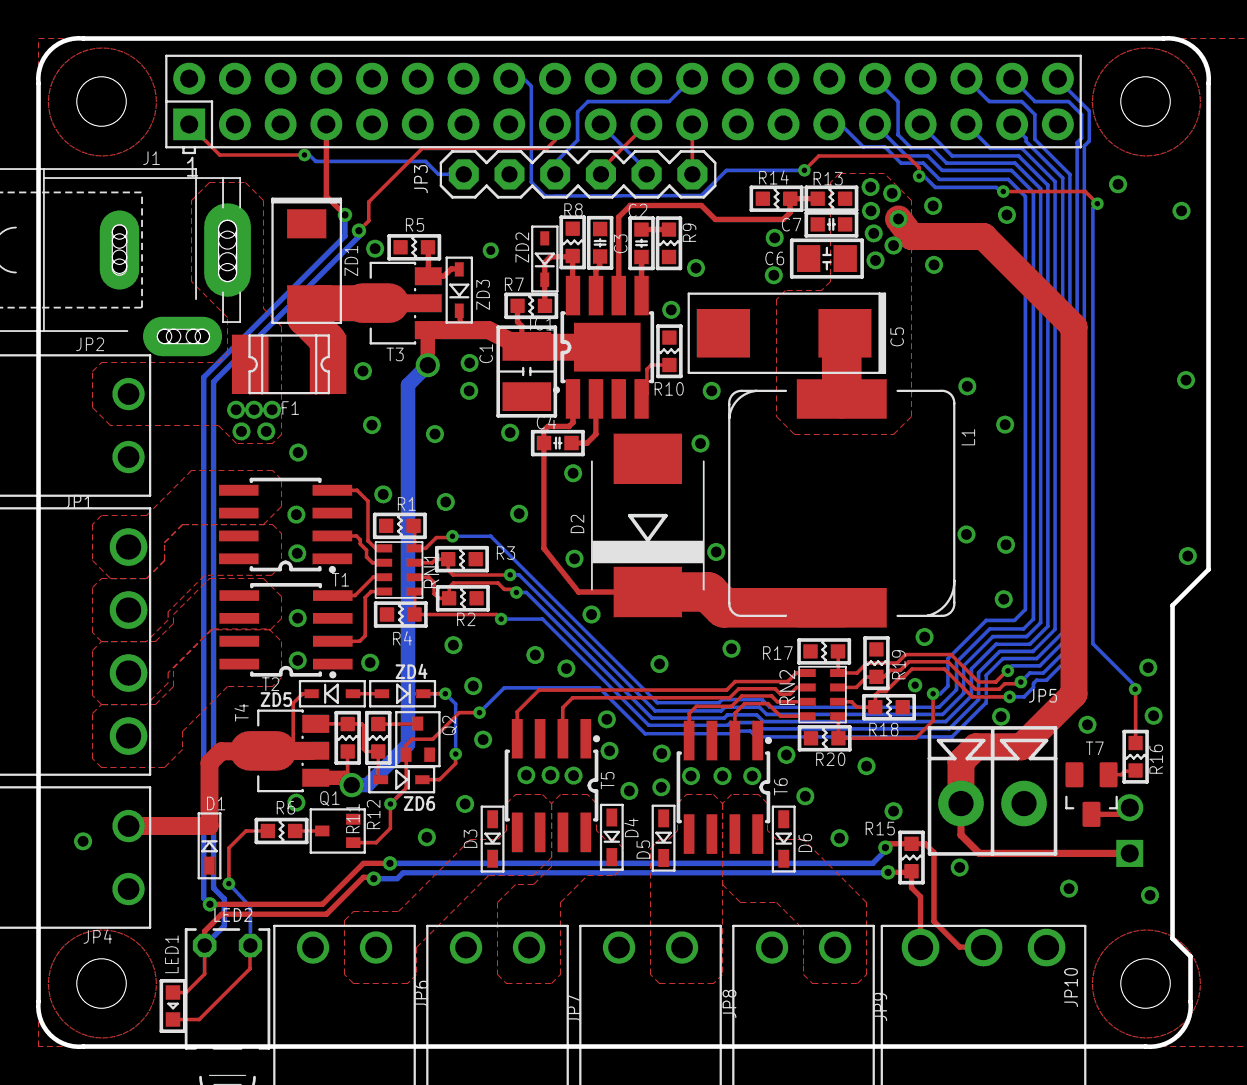
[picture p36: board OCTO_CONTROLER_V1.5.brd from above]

Board: 2 copper layers, 65.0 x 56.0 mm, 68 parts (1 on the bottom side), 55 nets.

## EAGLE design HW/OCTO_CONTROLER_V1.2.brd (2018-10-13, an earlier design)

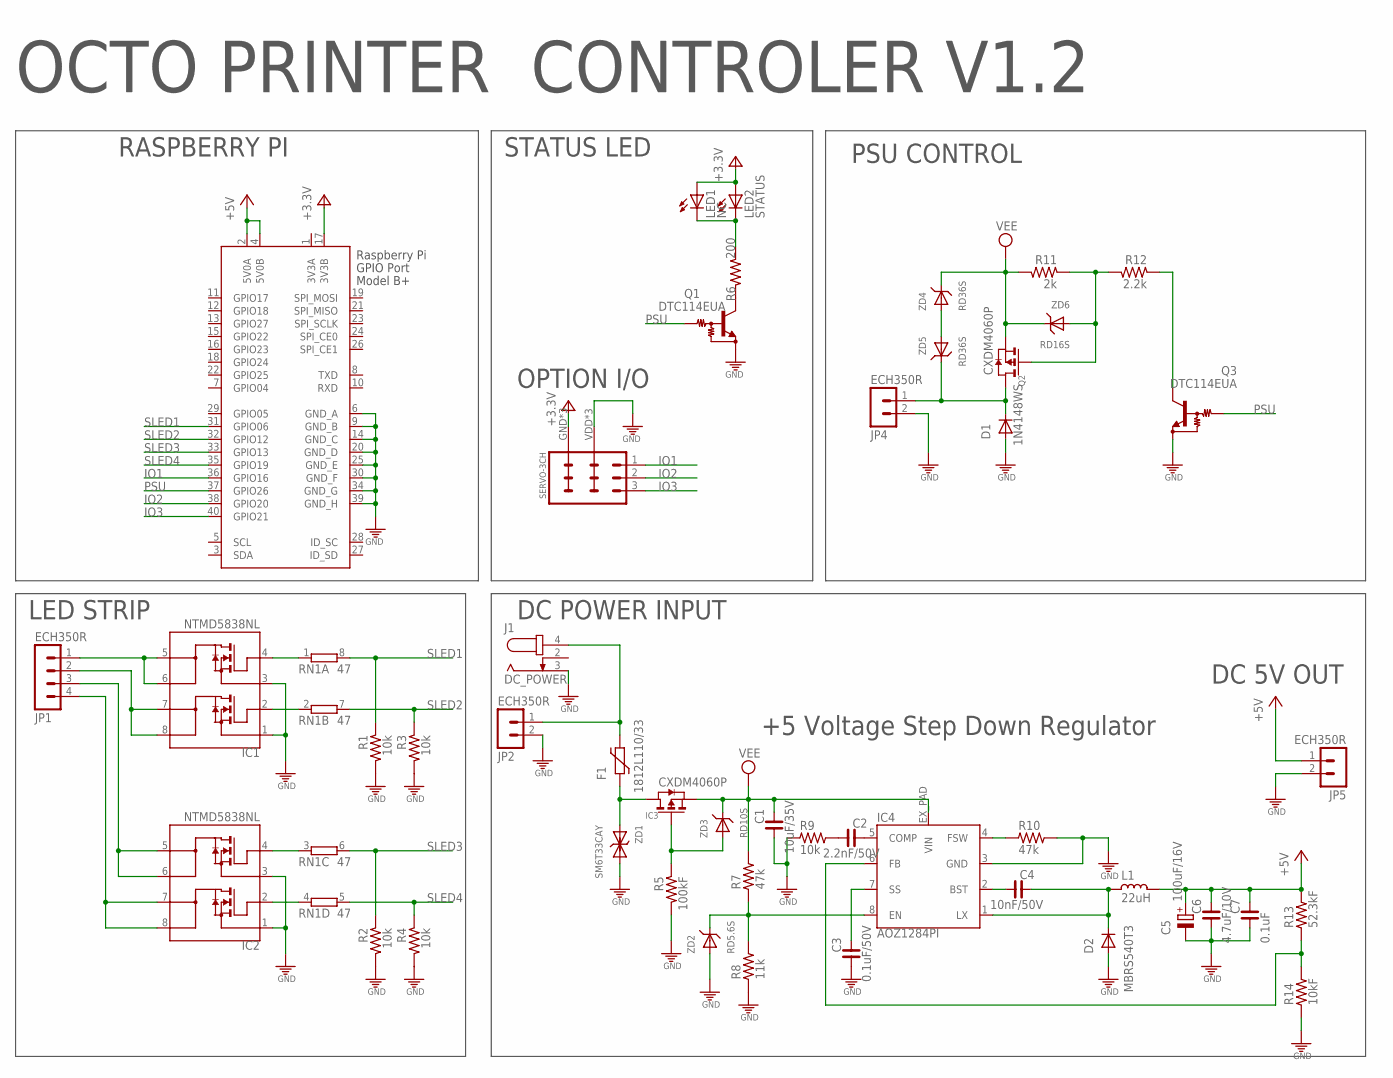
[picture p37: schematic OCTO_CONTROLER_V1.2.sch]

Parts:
C1: 10uF/35V; C3225
C2: 2.2nF/50V; C0603
C3: 0.1uF/50V; C0603
C4: 10nF/50V; C0603
C5: 100uF/16V; D/7343-31W
C6: 4.7uF/10V; C2012
C7: 0.1uF; C0603
D1: 1N4148WS; SOD323
D2: MBRS540T3; SMC
F1: 1812L110/33; 1812L
IC1, IC2: NTMD5838NL; SO08
IC3: CXDM4060P; SOT89
IC4: AOZ1284PI; S08-EP1
J1: DC_POWER; DC-005
JP1: ECH350R; ECH350R-04
JP2, JP4, JP5: ECH350R; ECH350R-02
JP3: SERVO-3CH; SERVO-3CH1
L1: 22uH; SHP1260P-F
LED1: NC; LED-1608
LED2: STATUS; 3FG2HD-T1
Q1, Q3: DTC114EUA; SC59-BEC
Q2: CXDM4060P; SOT89
R1, R2, R3, R4, R9: 10k; R0603
R5: 100kF; R0603
R6: 200; R0603
R7, R10: 47k; R0603
R8: 11k; R0603
R11: 2k; R0603
R12: 2.2k; R0603
R13: 52.3kF; R0603
R14: 10kF; R0603
RN1: 47; ARRAY_R3216
X1: RASPI_BOARD_B+#_F; RASPI_BOARD_B+_FULL
ZD1: SM6T33CAY; SMB
ZD2: RD5.6S; DSMM
ZD3: RD10S; DSMM
ZD4, ZD5: RD36S; DSMM
ZD6: RD16S; DSMM

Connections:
3V3: JP3.GND, JP3.GND@1 (GND), JP3.GND@2 (GND), LED1.A, LED2.A, X1.17 (3V3B)
3V3A: X1.1 (3V3A)
+5V: C5.+, C6.1, C7.1, JP5.1, L1.1, R13.2, X1.2 (5V0A), X1.4 (5V0B)
DC-IN: F1.P$1 (1), IC3.2 (D), IC3.2@1 (D), ZD1.A
GND: C1.2, C3.2, C5.-, C6.2, C7.2, D1.A, D2.A, IC1.1, IC1.3, IC2.1, IC2.3, IC4.3 (GND), J1.3 (1), JP2.2, JP3.VDD (+5V), JP3.VDD@1 (+5V), JP3.VDD@2 (+5V), JP4.2, JP5.2, Q1.1 (GND), Q3.1 (GND), R1.2, R2.2, R3.2, R4.2, R5.2, R8.1, R9.1, R10.2, R14.1, X1.6 (GND_A), X1.9 (GND_B), X1.14 (GND_C), X1.20 (GND_D), X1.25 (GND_E), X1.30 (GND_F), X1.34 (GND_G), X1.39 (GND_H), ZD1.C (K), ZD2.A
IO1: JP3.1, X1.36 (GPIO16)
IO2: JP3.2, X1.38 (GPIO20)
IO3: JP3.3, X1.40 (GPIO21)
unnamed: Q2.3 (G), R11.1, R12.2, ZD6.A
unnamed: LED1.C, LED2.K (C), R6.1
unnamed: ZD4.A, ZD5.A
unnamed: IC1.2, RN1.2 (1)
unnamed: IC1.4, RN1.1
unnamed: IC2.2, RN1.4 (1)
unnamed: IC4.6 (FB), R13.1, R14.2
unnamed: IC2.4, RN1.3 (1)
unnamed: C4.2, IC4.2 (BST)
unnamed: D1.C, JP4.1, Q2.2 (D), Q2.2@1 (D), ZD5.C
unnamed: C4.1, D2.C, IC4.1 (LX), L1.2
unnamed: IC4.4 (FSW), R10.1
unnamed: C3.1, IC4.7 (SS)
unnamed: IC4.8 (EN), R7.1, R8.2, ZD2.C
unnamed: C2.1, IC4.5 (COMP)
unnamed: Q3.3 (OUT), R12.1
unnamed: C2.2, R9.2
unnamed: Q1.3 (OUT), R6.2
unnamed: IC3.3 (G), R5.1, ZD3.A
unnamed: F1.P$2 (2), J1.4 (3), JP2.1
PSU: Q1.2 (IN), Q3.2 (IN), X1.37 (GPIO26)
S-LED1: IC1.5, IC1.6, JP1.1
S-LED2: IC1.7, IC1.8, JP1.2
S-LED3: IC2.5, IC2.6, JP1.3
S-LED4: IC2.7, IC2.8, JP1.4
SLED1: R1.1, RN1.8 (2), X1.31 (GPIO06)
SLED2: R3.1, RN1.7 (2), X1.32 (GPIO12)
SLED3: R2.1, RN1.6 (2), X1.33 (GPIO13)
SLED4: R4.1, RN1.5 (2), X1.35 (GPIO19)
VEE: C1.1, IC3.1 (S), IC4.EX_PAD (VIN), Q2.1 (S), R7.2, R11.2, ZD3.C, ZD4.C, ZD6.C

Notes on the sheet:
OCTO PRINTER CONTROLER V1.2
RASPBERRY PI
+5 Voltage Step Down Regulator
DC POWER INPUT
PSU CONTROL
STATUS LED
OPTION I/O
LED STRIP
DC 5V OUT

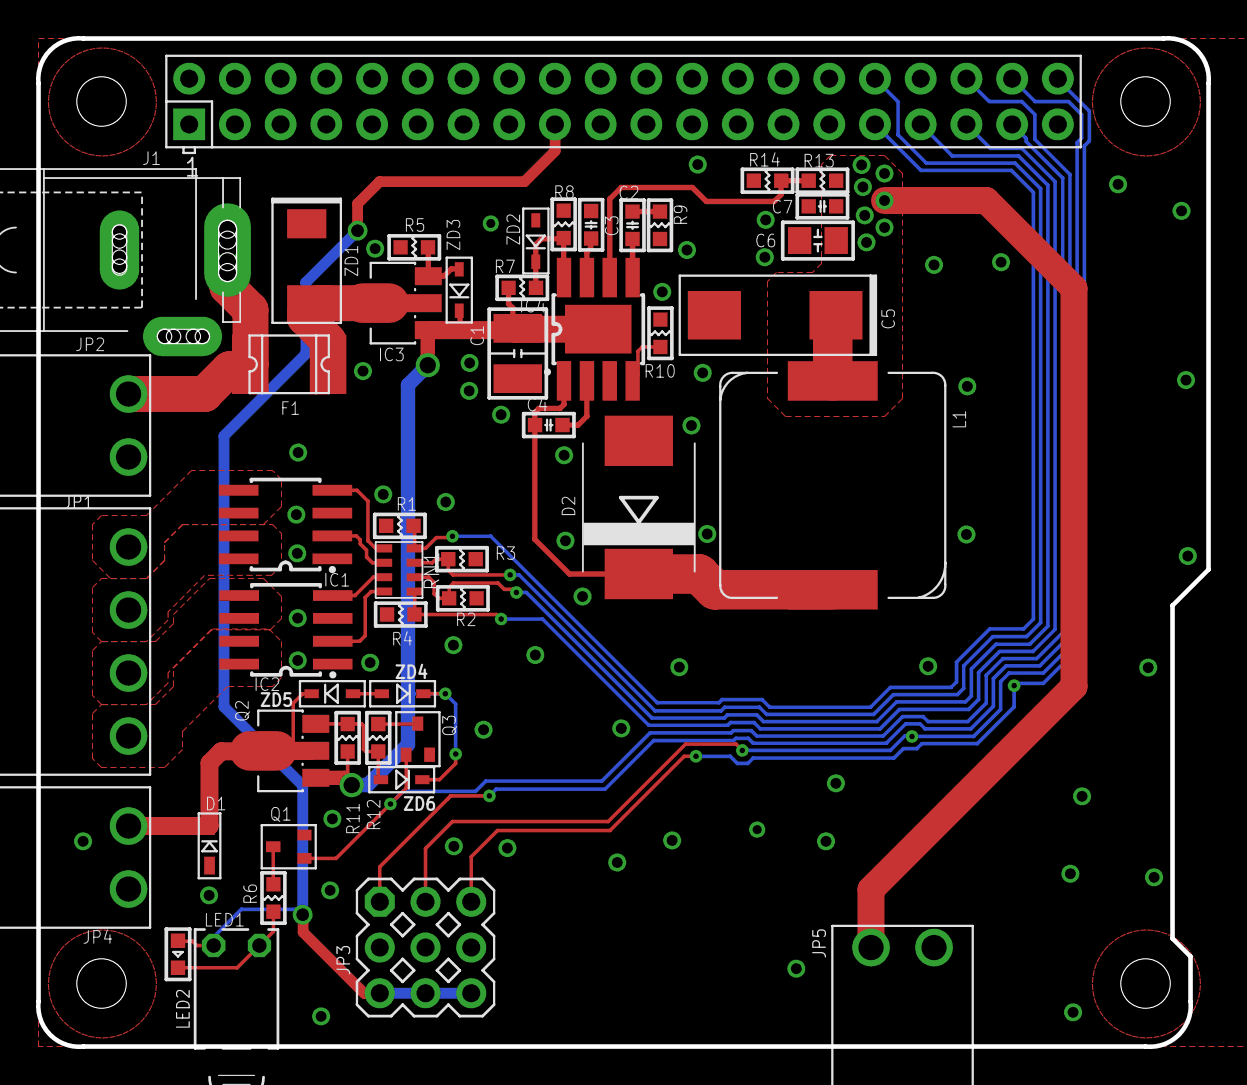
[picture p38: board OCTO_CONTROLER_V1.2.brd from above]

Board: 2 copper layers, 65.0 x 56.0 mm, 48 parts (0 on the bottom side), 37 nets.

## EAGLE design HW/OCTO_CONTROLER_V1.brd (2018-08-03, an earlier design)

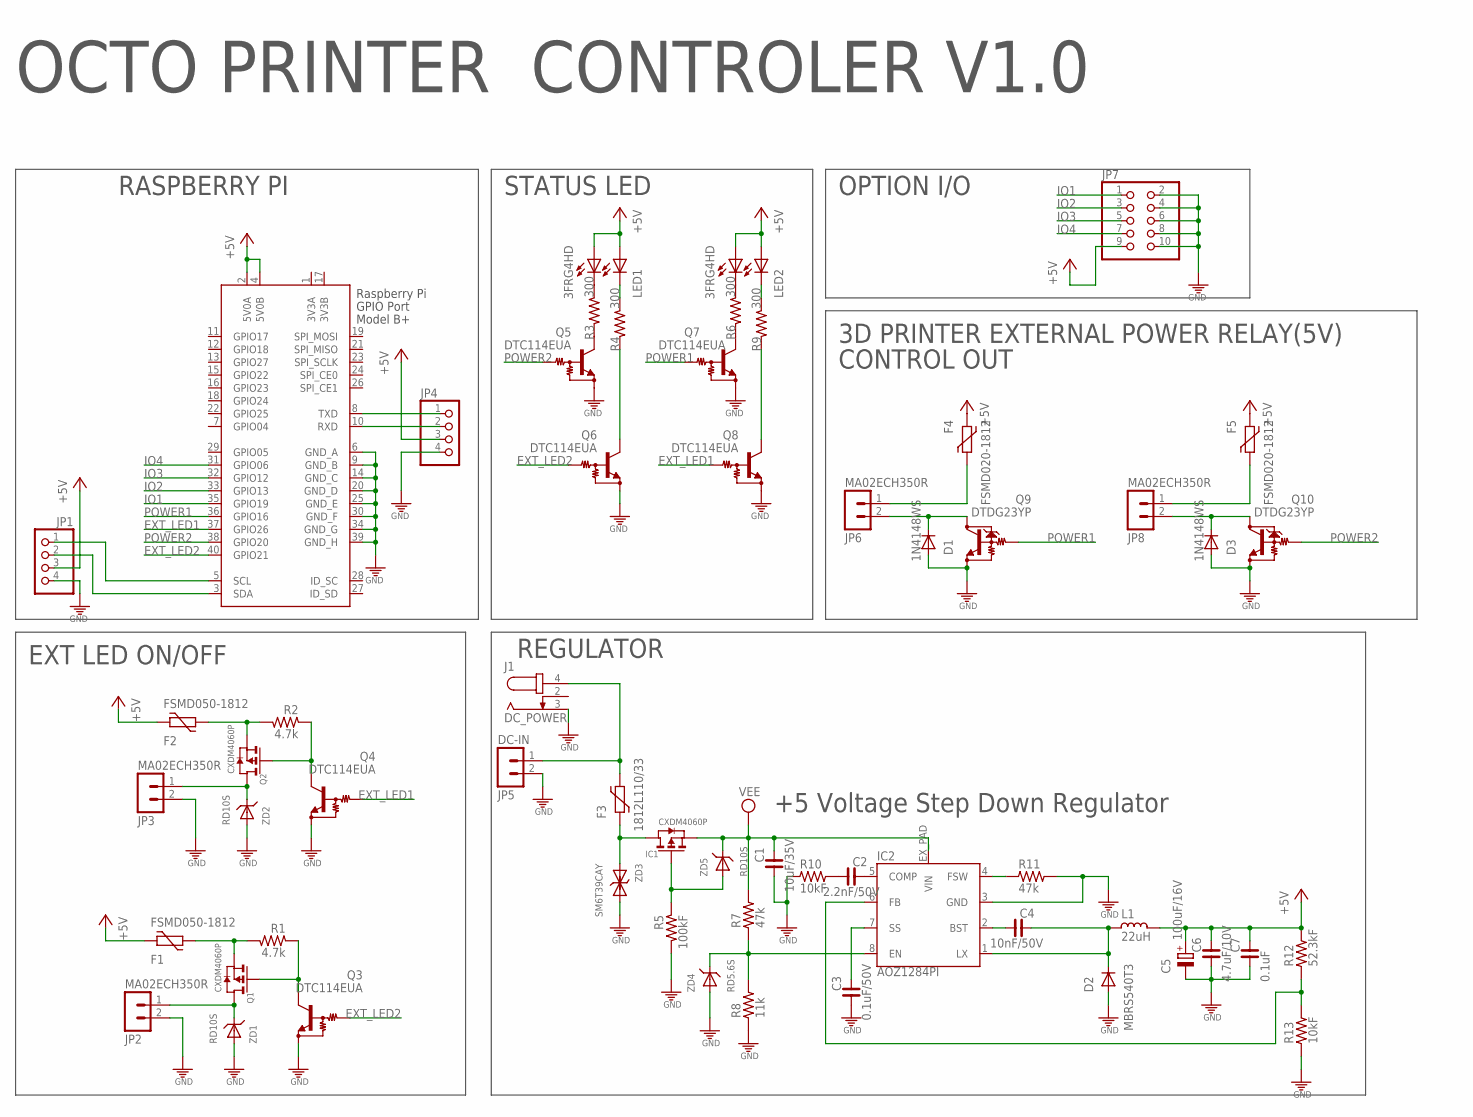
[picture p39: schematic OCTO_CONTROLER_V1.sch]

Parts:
C1: 10uF/35V; C3225
C2: 2.2nF/50V; C0603
C3: 0.1uF/50V; C0603
C4: 10nF/50V; C0603
C5: 100uF/16V; D/7343-31W
C6: 4.7uF/10V; C2012
C7: 0.1uF; C0603
D1, D3: 1N4148WS; SOD323
D2: MBRS540T3; SMC
F1, F2: FSMD050-1812; 1812L
F3: 1812L110/33; 1812L
F4, F5: FSMD020-1812; 1812L
IC1: CXDM4060P; SOT89
IC2: AOZ1284PI; S08-EP1
J1: DC_POWER; DC-005
JP1, JP4: PINHD-1X4; 1X04
JP2, JP3, JP6, JP8: MA02ECH350R; ECH350R-02
JP5: DC-IN; ECH350R-02
JP7: PINHD-2X5/90; 2X05/90
L1: 22uH; SHP1260P-F
LED1, LED2: 3FRG4HD; 3FRG4H
Q1, Q2: CXDM4060P; SOT89
Q3, Q4, Q5, Q6, Q7, Q8: DTC114EUA; SC59-BEC
Q9, Q10: DTDG23YP; MPT3
R1, R2: 4.7k; R0603
R3, R4, R6, R9: 300; R0603
R5: 100kF; R0603
R7, R11: 47k; R0603
R8: 11k; R0603
R10, R13: 10kF; R0603
R12: 52.3kF; R0603
X1: RASPI_BOARD_B+#_F; RASPI_BOARD_B+_FULL
ZD1, ZD2, ZD5: RD10S; DSMM
ZD3: SM6T39CAY; SMB
ZD4: RD5.6S; DSMM

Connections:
3V3A: X1.1 (3V3A)
3V3B: X1.17 (3V3B)
+5V: C5.+, C6.1, C7.1, F1.P$1 (1), F2.P$1 (1), F4.P$1 (1), F5.P$1 (1), JP1.3, JP4.3, JP7.9, L1.1, LED1.A (A1), LED1.A1 (A2), LED2.A (A1), LED2.A1 (A2), R12.2, X1.2 (5V0A), X1.4 (5V0B)
DC-IN: F3.P$1 (1), IC1.2 (D), IC1.2@1 (D), ZD3.A
EXT_LED1: Q4.2 (IN), Q8.2 (IN), X1.37 (GPIO26)
EXT_LED2: Q3.2 (IN), Q6.2 (IN), X1.40 (GPIO21)
GND: C1.2, C3.2, C5.-, C6.2, C7.2, D1.A, D2.A, D3.A, IC2.3 (GND), J1.3 (1), JP1.4, JP2.2, JP3.2, JP4.4, JP5.2, JP7.2, JP7.4, JP7.6, JP7.8, JP7.10, Q3.1 (GND), Q4.1 (GND), Q5.1 (GND), Q6.1 (GND), Q7.1 (GND), Q8.1 (GND), Q9.EMITTER (GND), Q10.EMITTER (GND), R5.2, R8.1, R10.1, R11.2, R13.1, X1.6 (GND_A), X1.9 (GND_B), X1.14 (GND_C), X1.20 (GND_D), X1.25 (GND_E), X1.30 (GND_F), X1.34 (GND_G), X1.39 (GND_H), ZD1.A, ZD2.A, ZD3.C (K), ZD4.A
IO1: JP7.1, X1.35 (GPIO19)
IO2: JP7.3, X1.33 (GPIO13)
IO3: JP7.5, X1.32 (GPIO12)
IO4: JP7.7, X1.31 (GPIO06)
unnamed: D1.C, JP6.2, Q9.COLLECTOR (OUT)
unnamed: Q1.3 (G), Q3.3 (OUT), R1.1
unnamed: JP2.1, Q1.2 (D), Q1.2@1 (D), ZD1.C
unnamed: F2.P$2 (2), Q2.1 (S), R2.2
unnamed: F1.P$2 (2), Q1.1 (S), R1.2
unnamed: D3.C, JP8.2, Q10.COLLECTOR (OUT)
unnamed: F5.P$2 (2), JP8.1
unnamed: F4.P$2 (2), JP6.1
unnamed: IC2.6 (FB), R12.1, R13.2
unnamed: JP1.1, X1.5 (SCL)
unnamed: C4.2, IC2.2 (BST)
unnamed: JP3.1, Q2.2 (D), Q2.2@1 (D), ZD2.C
unnamed: JP1.2, X1.3 (SDA)
unnamed: JP4.1, X1.8 (TXD)
unnamed: JP4.2, X1.10 (RXD)
unnamed: C4.1, D2.C, IC2.1 (LX), L1.2
unnamed: IC2.4 (FSW), R11.1
unnamed: C3.1, IC2.7 (SS)
unnamed: IC2.8 (EN), R7.1, R8.2, ZD4.C
unnamed: C2.1, IC2.5 (COMP)
unnamed: Q2.3 (G), Q4.3 (OUT), R2.1
unnamed: C2.2, R10.2
unnamed: Q5.3 (OUT), R3.2
unnamed: LED1.K (C1), R3.1
unnamed: LED1.K1 (C2), R4.1
unnamed: Q7.3 (OUT), R6.2
unnamed: LED2.K (C1), R6.1
unnamed: LED2.K1 (C2), R9.1
unnamed: Q8.3 (OUT), R9.2
unnamed: Q6.3 (OUT), R4.2
unnamed: IC1.3 (G), R5.1, ZD5.A
unnamed: F3.P$2 (2), J1.4 (3), JP5.1
POWER1: Q7.2 (IN), Q9.BASE (IN), X1.36 (GPIO16)
POWER2: Q5.2 (IN), Q10.BASE (IN), X1.38 (GPIO20)
VEE: C1.1, IC1.1 (S), IC2.EX_PAD (VIN), R7.2, ZD5.C

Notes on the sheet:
OCTO PRINTER CONTROLER V1.0
EXT LED ON/OFF
RASPBERRY PI
+5 Voltage Step Down Regulator
REGULATOR
3D PRINTER EXTERNAL POWER RELAY(5V)
STATUS LED
OPTION I/O
CONTROL OUT

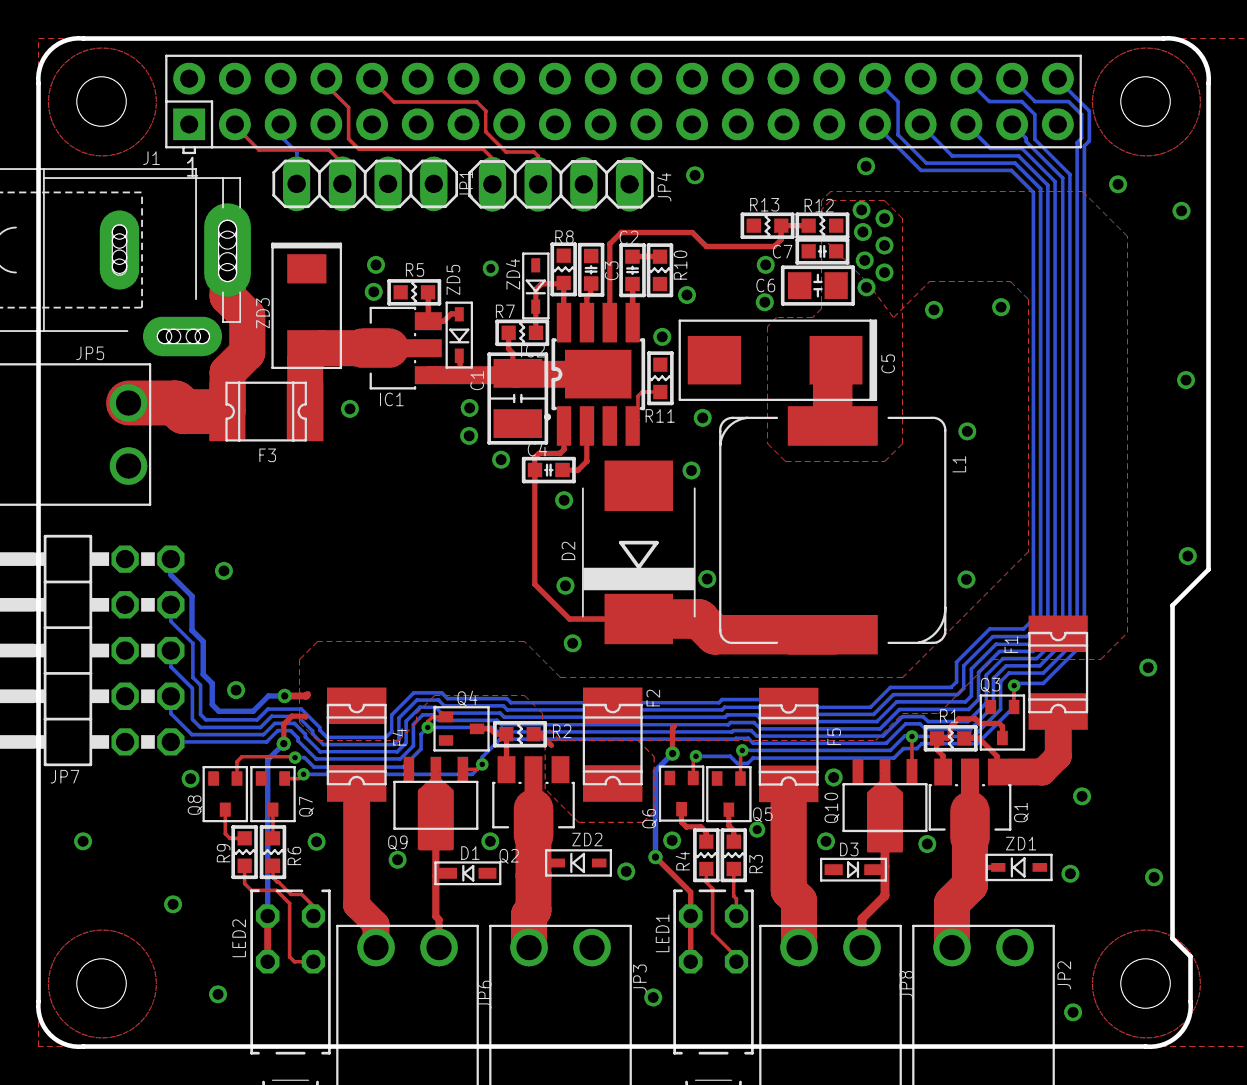
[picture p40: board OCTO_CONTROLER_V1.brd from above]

Board: 2 copper layers, 65.0 x 56.0 mm, 58 parts (0 on the bottom side), 44 nets.

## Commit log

2018-07-23 PCB DESIGNE UPDATE
    [3D_PRINTER_SHILED_V1.brd, 3D_PRINTER_SHILED_V1.sch]
2018-07-23 RENAME PCB DESIGN FILE
    [OCTO_CONTROLER_V1.brd, OCTO_CONTROLER_V1.sch]
2018-08-03 LED 저항값 수정
    [OCTO_CONTROLER_V1.brd, OCTO_CONTROLER_V1.sch]
2018-09-04 OCTO PRINTER V1.2 PCB DESIGN
    [OCTO_CONTROLER_V1.1.brd, OCTO_CONTROLER_V1.1.sch]
2018-09-04 v1.1 pcb gerber
    [OCTO_CONTROLER_V1.1.brd, OCTO_CONTROLER_V1.1.sch]
2018-09-10 거버업로드
    [OCTO_CONTROLER_V1.1.brd, OCTO_CONTROLER_V1.1.sch]
2018-10-02 v1.1수정
    [OCTO_CONTROLER_V1.1.brd]
2018-10-12 v1.1 pcb
    image up load
2018-10-13 BOM & V1.2 PCB UPDATE
    [OCTO_CONTROLER_V1.2.brd, OCTO_CONTROLER_V1.2.sch, OCTO_CONTROLER_V1.2_BOM.xlsm]
2018-10-13 pcb v1.2 silk update
    [OCTO_CONTROLER_V1.2.brd]
2018-10-19 파일 정리
2018-10-20 bom pdf version update
    [OCTO_CONTROLER_V1.2_BOM.xlsm]
2018-10-20 WIWRING MENUAL UPDATE
    [OCTO_CONTROLER_V1.2_BOM.xlsm]
2018-11-03 V1.3 PCB UPDATE
    ENCLOSURE-CONTROL PART ADD-ON
    [OCTO_CONTROLER_V1.3.brd, OCTO_CONTROLER_V1.3.sch]
2018-11-03 V1.3 PCB PATHC
    DHT-22 PULL-UP 10k->4.7K
    [OCTO_CONTROLER_V1.3.brd, OCTO_CONTROLER_V1.3.sch]
2018-11-05 V1.3 PCB SILK UPDATE
2018-12-05 V1.3 PCB IMAGE UPDATE
2020-11-28 octo printer controler v1.4 update
    klipper support(adxl345)
    Raspberry Pi AP Cooling Fan Support
    [OCTO_CONTROLER_V1.2_BOM.xlsm, OCTO_CONTROLER_V1.4.brd, OCTO_CONTROLER_V1.4.sch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]
2020-11-28 v1.4 circuit pdf file upload
    [OCTO_CONTROLER_V1.4_BOM.xlsm]
2020-11-28 Organize files
    [OCTO_CONTROLER_V1.2_BOM.xlsm, OCTO_CONTROLER_V1.4_BOM.xlsm]
2020-11-28 V1.4 BOM UPDATE
    [OCTO_CONTROLER_V1.4_BOM.xlsm]
2021-07-17 notebook change
    [OCTO_CONTROLER_V1.5.brd, OCTO_CONTROLER_V1.5.sch]
2021-10-12 정기업로드
    정기업로드
    [OCTO_CONTROLER_V1.5.brd, OCTO_CONTROLER_V1.5.sch]
